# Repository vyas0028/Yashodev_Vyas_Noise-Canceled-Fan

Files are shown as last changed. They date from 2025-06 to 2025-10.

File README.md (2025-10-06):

# Noise Canceling Fan Project

A desktop fan that cancels its own noise using active noise cancellation, built utilizing CAD, embedded programming, signal processing, and acoustic analysis to create a standalone product! 

<div style="display: flex; justify-content: center; align-items: center; gap: 50px;">
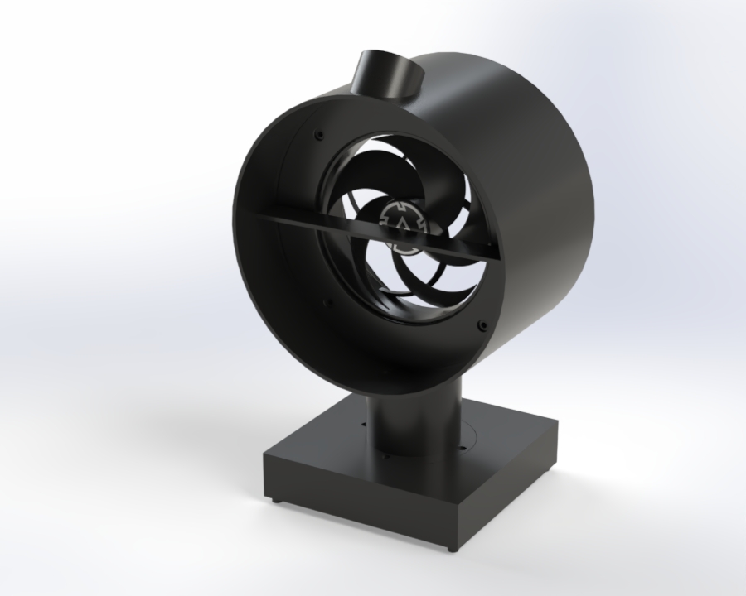
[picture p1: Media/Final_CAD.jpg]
Final CAD model of fan
  
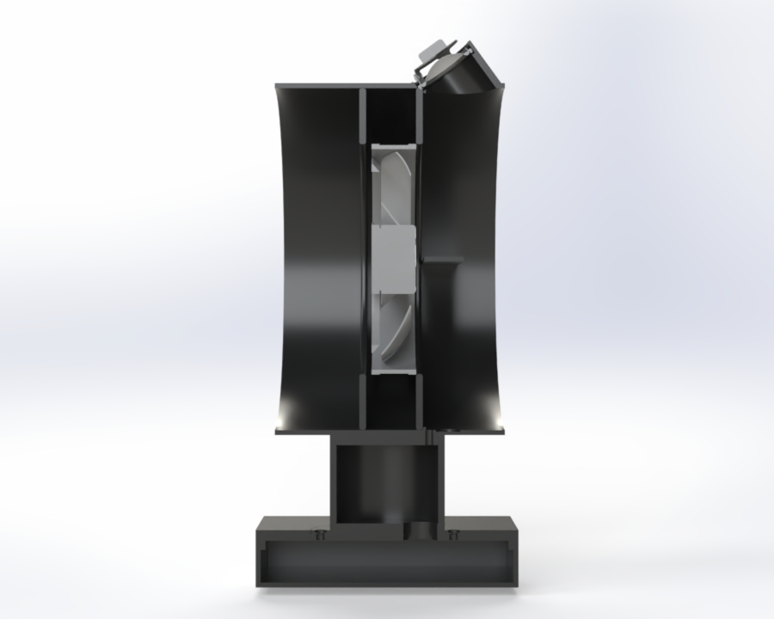
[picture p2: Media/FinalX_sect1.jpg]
Cross-section of fan CAD model
  
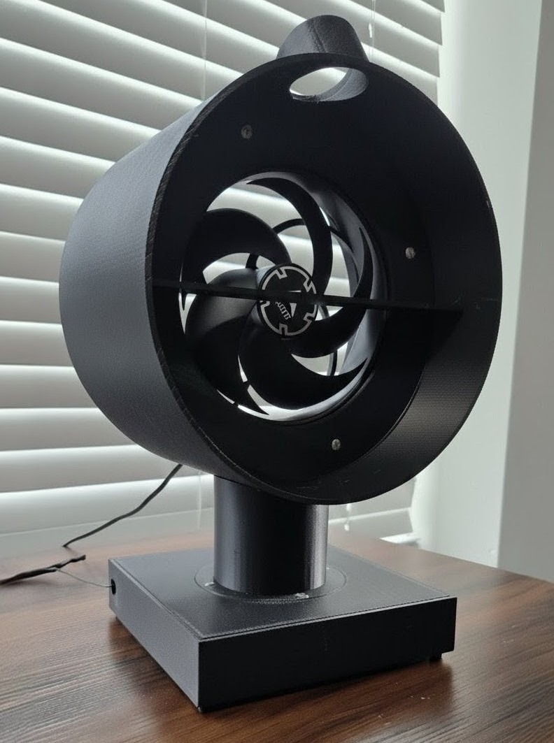
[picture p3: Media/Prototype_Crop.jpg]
Photo of physical fan prototype
  
</div>

---

## What It Does

This fan detects its own blade-generated noise using a microphone, identifies the dominant frequency using an FFT (Fast Fourier Transform), and cancels it in real time by outputting inverted sound through a speaker

---

## How it Works  
1. The microcrophone and Teensy microcontroller communicate using I2S
2. The noise data that is sent to the microcontroller from the mic is processed by an FFT (Fast Fourier Transform) in the PJRC Audio library.
   - This identifies the specific frequency of noise with the highest amplitude
4. Once the specific frequency is identified, the tone is phase shifted 180 deg and played out of the speaker using AudioConnection 
5. A simple hill-climb/coordinate descent algorithm reads the FFT again and nudges the phase + amplitude of the anti-tone up and down until a minimum is achieved.  

---

## Testing 
- Ran modal FEA to ensure that the housing doesn't resonate at the fan's blade pass frequency of 172 Hz.
    - Found main vibrational mode at 350 Hz. Well out of range for resonance.
- Conducted bench testing
    - Wired Teensy, speaker + amp, microphone, and fan together. Consolidated grounds and ensured that microphone can record audio that can be played out of the speaker. Also ensured that fan can be properly controlled via PWM. 
## Status/Next Steps
- Bench testing is now complete. All components - speaker, mic, Teensy, and fan connect to each other and are functonal on the breadboard and mechanically fit into the shroud and base. 
- Next steps will be rewiring everything into the 3D printed housing, taking decibel measurements, refining the algorithm (implement active FxLMS, possibly replace FFT with Goertzel), and creating a PCB to replace the breadboard.

---

## CAD Model Links
| [Part](link)                                                      |   Description  
| [Box](CAD/Project_CAD/box.SLDPRT)                                 |   Box that forms the base. Houses electronics.   
| [Lid](CAD/Project_CAD/lid.SLDPRT)                                 |   Lid that fits flush with top of base. Mounts to support tube with screws.  
| [Support_Tube](CAD/Project_CAD/tube.SLDPRT)                       |   Vertical support tube that rises from lid to shroud. Houses wiring.   
| [Fan_Housing_Front_Plate](CAD/Project_CAD/Fan_Front_Plate.SLDPRT) |   Circular plate that sits in front of fan to create circular profile to fit into shroud.   
| [Fan_Housing_Back_Plate](CAD/Project_CAD/Fan_Back_Plate.SLDPRT)   |   Circular plate that sits in behind fan to create circular profile to fit into shroud.   
| [Fan_Shroud](CAD/Project_CAD/Shroud.SLDPRT)                       |   Horizontal cylinder that houses fan, microphone, and speaker. Connects to support tube at bottom.      
| [Final_Assembly](CAD/Project_CAD/Final_Assembly.SLDPRT)           |   Final assembly of shroud, tubewith holes, lid, and base.

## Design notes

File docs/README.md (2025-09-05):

# Noise Canceling Fan Readme

A desktop fan that actively reduces its own noise using real-time noise cancellation. This project combines CAD, embedded programming, signal processing, and acoustic analysis to showcase the engineering process from start to finish and create a standalone product! 

<p float="left">
  
  
</p>

---

## What It Does

This fan detects its own blade-generated noise using a microphone, identifies the dominant frequency using an FFT (Fast Fourier Transform), and cancels it in real time by outputting inverted sound through a speaker

---

## How it Works  
1. The microcrophone and Teensy microcontroller communicate using I2S
2. The noise data that is sent to the microcontroller from the mic is processed by an FFT (Fast Fourier Transform) in the PJRC Audio library.
   - This identifies the specific frequency of noise with the highest amplitude
4. Once the specific frequency is identified, the tone is phase shifted 180 deg and played out of the speaker using AudioConnection 
5. A simple hill-climb/coordinate descent algorithm reads the FFT again and nudges the phase + amplitude of the anti-tone up and down until a minimum is achieved.  

---

## Status/Next Steps
- Bench testing is now complete. All components - speaker, mic, Teensy, and fan connect to each other and are functonal on the breadboard and mechanically fit into the shroud and base. 
- Next steps will be rewiring everything into the 3D printed housing, taking decibel measurements, refining the algorithm (implement active FxLMS, possibly replace FFT with Goertzel), and creating a PCB to replace the breadboard.

---

## CAD Model Links
| [Part](link)                                                      |   Description  
| [Box](CAD/Project_CAD/box.SLDPRT)                                 |   Box that forms the base. Houses electronics.   
| [Lid](CAD/Project_CAD/lid.SLDPRT)                                 |   Lid that fits flush with top of base. Mounts to support tube with screws.  
| [Support_Tube](CAD/Project_CAD/tube.SLDPRT)                       |   Vertical support tube that rises from lid to shroud. Houses wiring.   
| [Fan_Housing_Front_Plate](CAD/Project_CAD/Fan_Front_Plate.SLDPRT) |   Circular plate that sits in front of fan to create circular profile to fit into shroud.   
| [Fan_Housing_Back_Plate](CAD/Project_CAD/Fan_Back_Plate.SLDPRT)   |   Circular plate that sits in behind fan to create circular profile to fit into shroud.   
| [Fan_Shroud](CAD/Project_CAD/Shroud.SLDPRT)                       |   Horizontal cylinder that houses fan, microphone, and speaker. Connects to support tube at bottom.      
| [Final_Assembly](CAD/Project_CAD/Final_Assembly.SLDPRT)           |   Final assembly of shroud, tubewith holes, lid, and base.

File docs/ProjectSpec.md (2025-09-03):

## Welcome to the Noise Canceling Fan Project Specification! This is a a summary of general project parameters. 

## Project Overview
A desktop fan assembly that actively cancels its own noise by collecting noise signal using MEMS microphone, conducting FFT on a Teensy microcontroller, and then outputting an inverted signal through a speaker to cancel fan whine. 

---

## Design Inputs
- Microphone must detect fan noise frequencies and communicate with Teensy. 
- Teensy must perform real-time FFT and generate inverted wave through speaker.
- The fan must fit snugly into a circular chamber.
- The base must allow for a breadboard/pcb to sit inside.
- There must be a way to prevent direct feedback from the speaker into the mic.

---

## Performance Targets

| Metric | Target Value |
|---|---|
| SPL Reduction (@ mic) | ≥ 4 dB |
| Fan Speed Range | 200–1700 RPM |
| FFT Latency | ≤ 50 ms |

---

## Mechanical Spec
- **Fan**: 140 mm ARCTIC P14 PWM, enclosed in horizontal cylindrical shell
- **Support**: Cylindrical post connecting fan shell to base
- **Base**: 120 × 120 × 30 mm rectangular platform with hollow interior
- **Mic**: Top surface of base, centered in front of fan
- **Speaker**: Front face of base in circular cutout
- **Feet**: 4 corner supports with rubber bottoms for grip

---

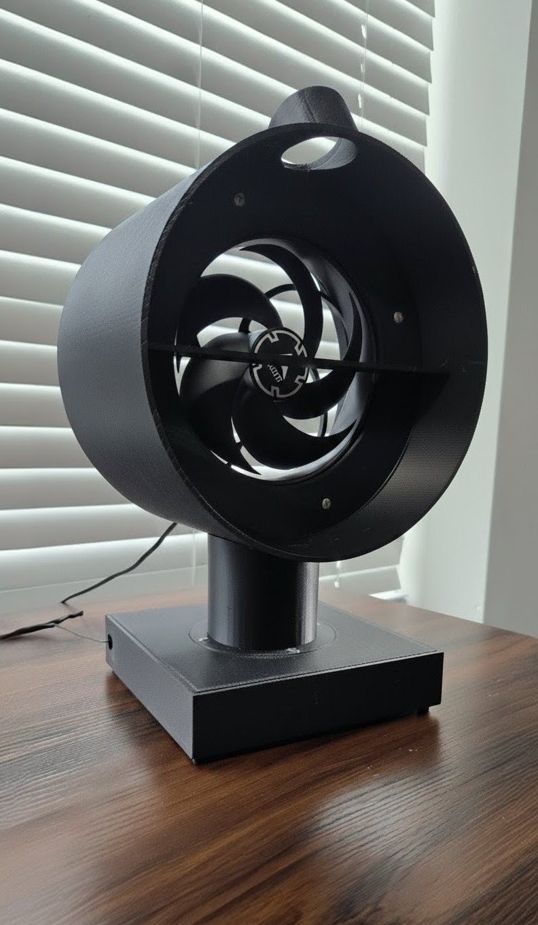
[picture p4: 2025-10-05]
Media/Prototype.jpg

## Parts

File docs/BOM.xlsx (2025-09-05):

Item # | Part / Description | Manufacturer | Part # | Qty | Unit Price (USD) | Vendor Link | Status
1 | Teensy 4.1 (with headers) | PJRC | TEENSY41 | 1 | 29.95 | https://www.pjrc.com/store/teensy41.html | Ordered
2 | INMP441 MEMS I²S Microphone Module (5‑pack) | InvenSense | INMP441‑MOD | 1 | 7.99 | https://www.amazon.com/dp/B086KQ4DLG | Ordered
3 | MAX98357A I²S Class‑D Audio Amp (4‑pack) | Maxim/ADI | MAX98357A‑MOD | 1 | 8.89 | https://www.amazon.com/dp/B075N8248Q | Ordered
4 | 40 mm 4 Ω 3 W Full‑Range Speaker (pair) | Gikfun | EK1794 | 1 | 6.99 | https://www.amazon.com/dp/B01L8GHB7O | Ordered
5 | ARCTIC P14 PWM PST 140 mm Fan | Arctic | ACFAN00137A | 1 | 10.99 | https://www.amazon.com/dp/B07GJZG3RZ | Owned
6 | 12 V 2 A DC Power Adapter (barrel jack) | HighPot | 12V2A‑ADP | 1 | 8.49 | https://www.amazon.com/dp/B01MEF5MHQ | Owned
7 | Barrel Jack to Screw Terminal Adapter | Uxcell | 214‑BJ‑ST | 1 | 4.99 | https://www.amazon.com/dp/B07WJ3N2ZK | Ordered
8 | USB‑C Wall Brick 5 V 2 A + Cable | Anker | A2017 | 1 | 11.99 | https://www.amazon.com/dp/B07THHQMHM | Owned
9 | Breadboard + Jumper Wires | Elegoo | EL‑CP‑004 | 1 | 6.99 | https://www.amazon.com/dp/B01EV70C78 | Owned
10 | M3 Heat‑Insert Brass Inserts (50 pcs) | E‑Sun | M3‑INS‑50 | 1 | 9.99 | https://www.amazon.com/dp/B07B4WPNJF | Planned
11 | Rubber Feet, 12 mm (set of 4) | 3M | SJ5303 | 1 | 3.5 | https://www.amazon.com/dp/B0006HVMGQ | Planned

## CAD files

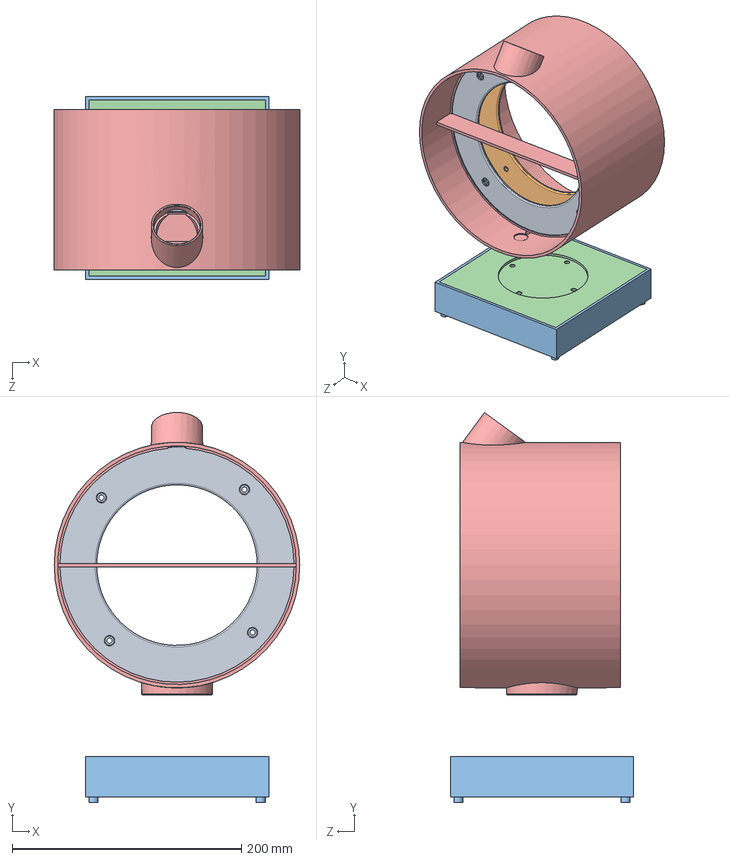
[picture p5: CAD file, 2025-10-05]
CAD/Project_CAD/Assemblies/FINAL_assembly.SLDASM
214.3 x 340.4 x 160.0 mm
Shroud
lid
Fan_Back_Plate
Fan_Front_Plate

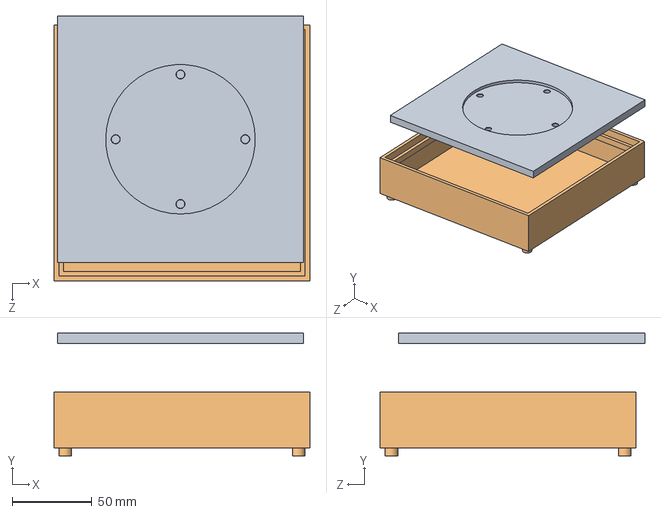
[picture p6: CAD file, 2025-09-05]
CAD/Project_CAD/Assemblies/box+lid_for_Image.SLDASM
160.0 x 76.9 x 165.5 mm
lid

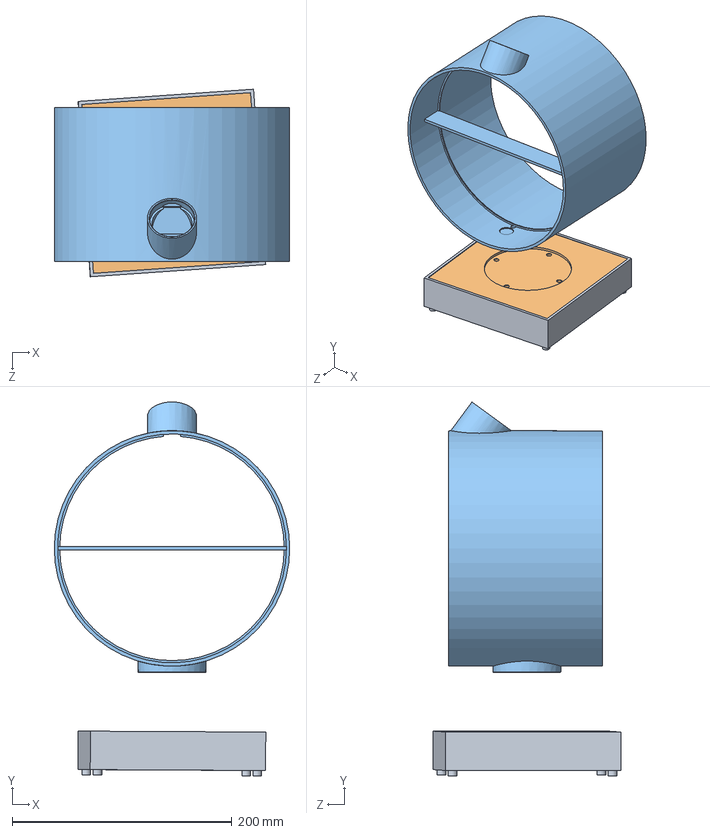
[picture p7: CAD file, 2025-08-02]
CAD/Project_CAD/Test_Assembly.SLDASM
214.3 x 340.4 x 170.7 mm
Shroud
lid

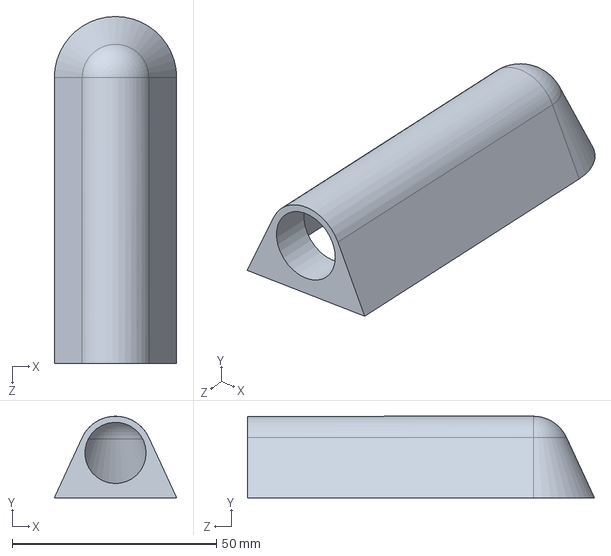
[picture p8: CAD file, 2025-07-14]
CAD/Practice_CAD/Practice_Lampshade.SLDPRT
30.0 x 20.0 x 85.0 mm

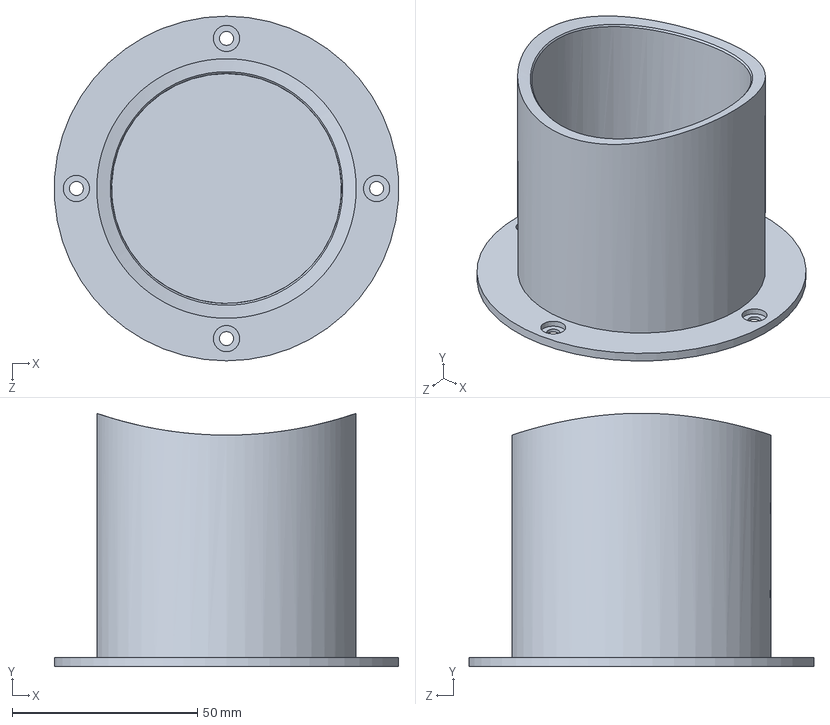
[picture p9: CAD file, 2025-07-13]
CAD/Project_CAD/Parts_For_Printing/Tube+shroud.SLDPRT
92.8 x 68.4 x 93.0 mm

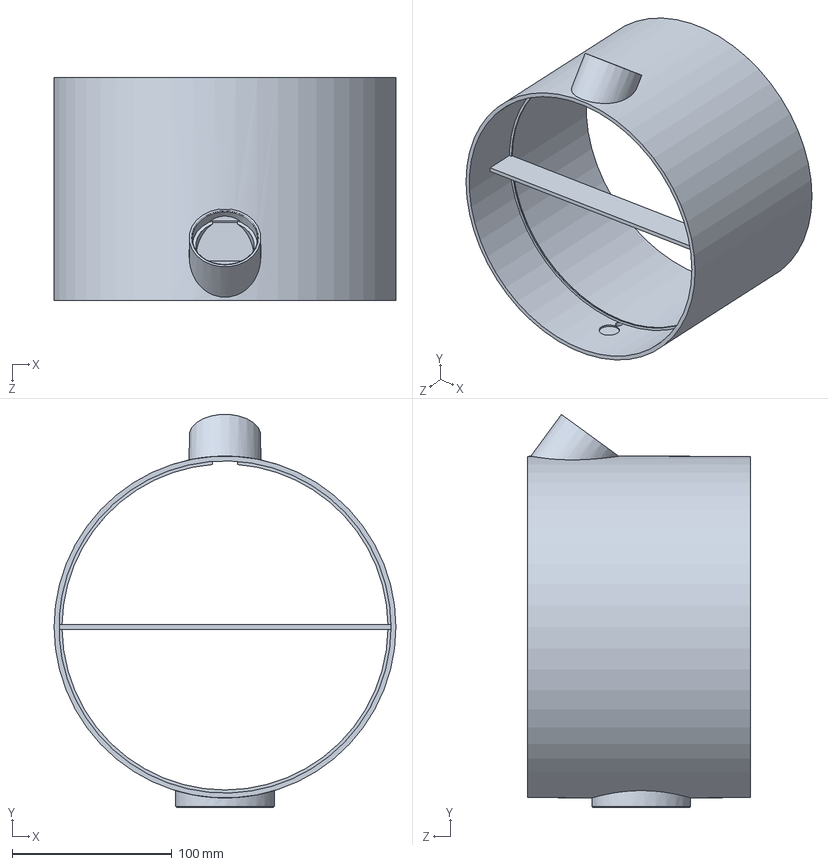
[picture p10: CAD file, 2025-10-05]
CAD/Project_CAD/Shroud.SLDPRT
214.3 x 246.4 x 140.0 mm

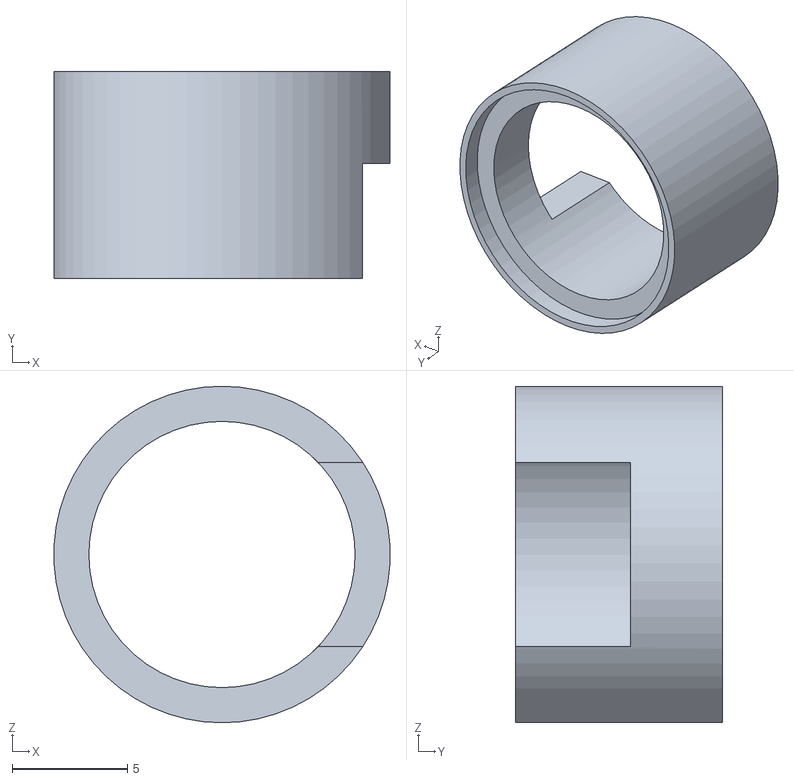
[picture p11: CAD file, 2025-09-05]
CAD/STL_Files/Mic_Fixture.STL
14.6 x 9.00 x 14.6

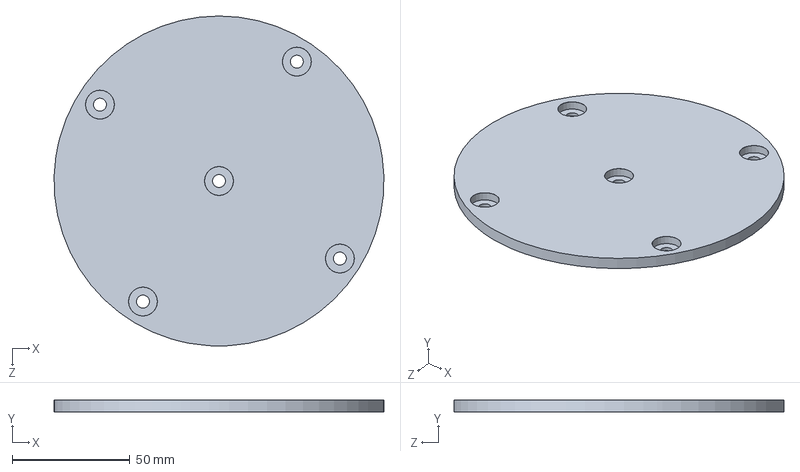
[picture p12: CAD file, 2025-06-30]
CAD/Practice_CAD/Practice_Plate.SLDPRT
139.9 x 5.00 x 140.0 mm

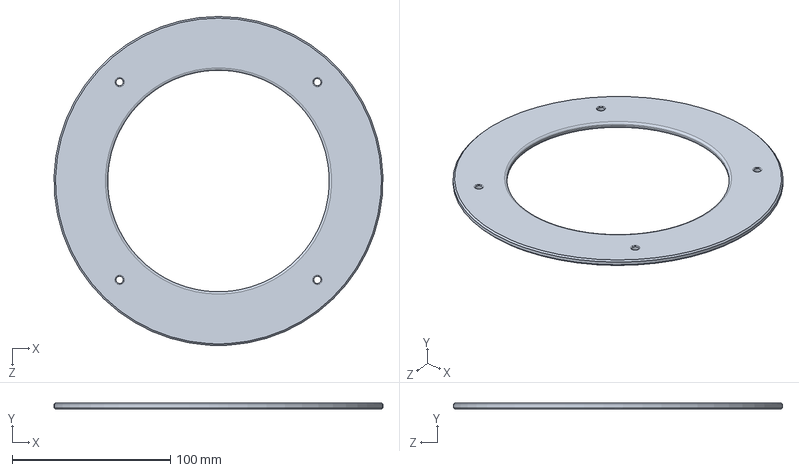
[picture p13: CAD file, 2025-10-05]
CAD/Project_CAD/Fan_Back_Plate.SLDPRT
207.9 x 4.00 x 208.0 mm

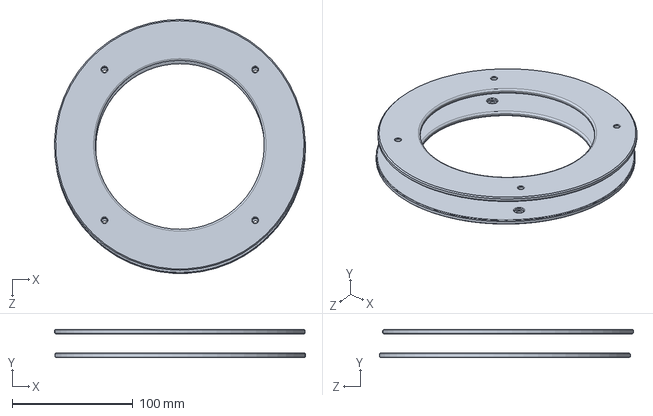
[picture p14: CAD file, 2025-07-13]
CAD/Project_CAD/Parts_For_Printing/Assem8.SLDPRT
208.2 x 23.6 x 210.7 mm

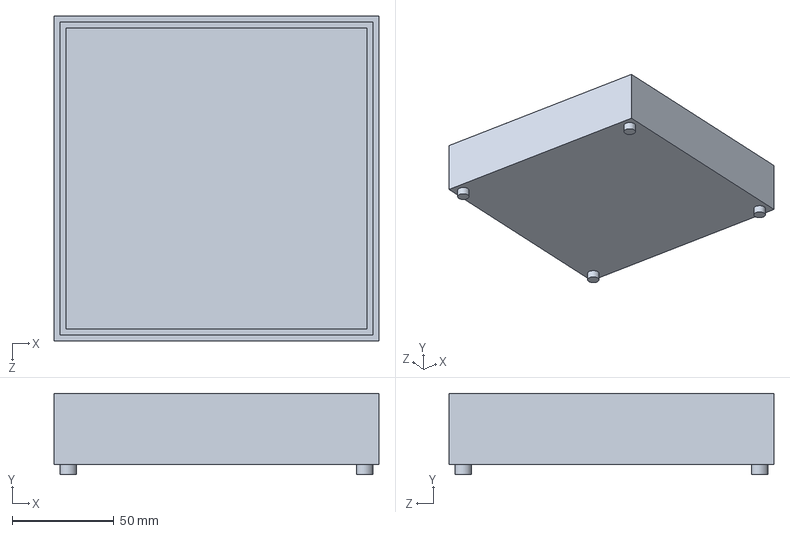
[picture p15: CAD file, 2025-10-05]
CAD/Project_CAD/box.SLDPRT
160.0 x 40.0 x 160.0 mm

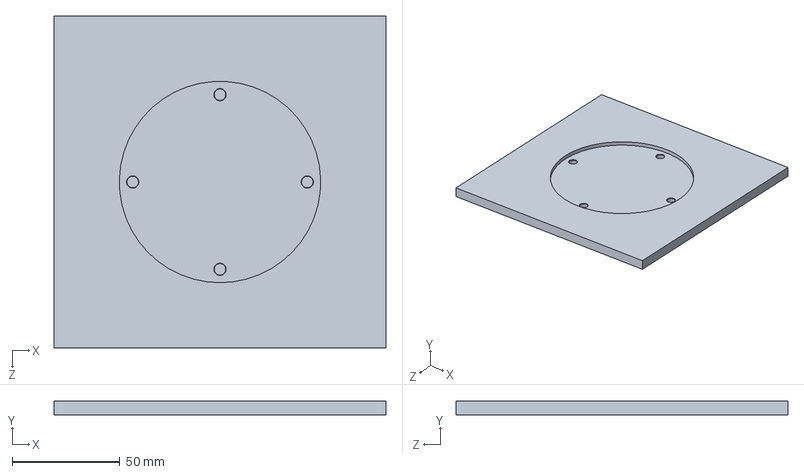
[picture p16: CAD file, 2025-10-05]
CAD/Project_CAD/lid.SLDPRT
154.0 x 6.50 x 154.0 mm

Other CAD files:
CAD/Project_CAD/Assemblies/X_section.SLDASM
CAD/STL_Files/tube.STL
CAD/STL_Files/Fan_Back_Plate.STL
CAD/Project_CAD/Fan_Front_Plate.SLDPRT
CAD/STL_Files/box.STL
CAD/Project_CAD/Mic_Fixture.SLDPRT
CAD/Project_CAD/tube.SLDPRT
CAD/STL_Files/Assem2.SLDPRT
CAD/STL_Files/Assem8.STL
CAD/STL_Files/Fan_Front_Plate.STL
CAD/STL_Files/Shroud.STL
CAD/STL_Files/lid.STL

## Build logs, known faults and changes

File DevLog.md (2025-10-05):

# Noise-Canceling Fan Devlog

Welcome to the Noise-Canceling Fan DevLog! This is a running summary of daily work on this project.

---

## 06-29-2025

**Done**  
- Created Repo and README  
- Brainstormed high-level design: 3D printed hollow rectangular base with four supports, speaker on the front face, microphone hole on the top face, fan housed in horizontal cylinder supported by cylindrical column from base. Electrical housed under the base.

**Learned**  
- GitHub repo organizations for engineering projects.

**Next**  
- Order parts (mic, speaker, Teensy, etc), CAD practice, write project specifications.

---

## 06-30-2025

**Done**  
- Ordered parts (microcontroller, fan, electronics)

**Learned**  
- Electronics required (amplifier module, barrel jack adapter, etc)

**Next**  
- Write spec, BOM, CAD practice

---

## 07-02-2025

**Done**  
- Got hung up on internship work. Watched one SolidWorks recap video.

**Next**  
- CAD practice, first models.

---

## 07-03-2025

**Done**  
- Completed SolidWorks recap video

**Learned**  
- Reviewed SolidWorks basics (sketching, boss/revolve, shell, fillet)

**Next**  
- Begin practice parts

---

## 07-06-2025

**Done**  
- Created horizontal “lampshade” example from SolidWorks part modeling tutorial utilizing sketch, extrude, extrude-cut, shell, and fillet.  
  - [Practice_Lampshade.SLDPRT](../CAD/Practice_CAD/Practice_Lampshade.SLDPRT)  
- Created circular baseplate to practice HoleWizard  
  - [Practice_Plate.SLDPRT](../CAD/Practice_CAD/Practice_Plate.SLDPRT)

<p float="left">
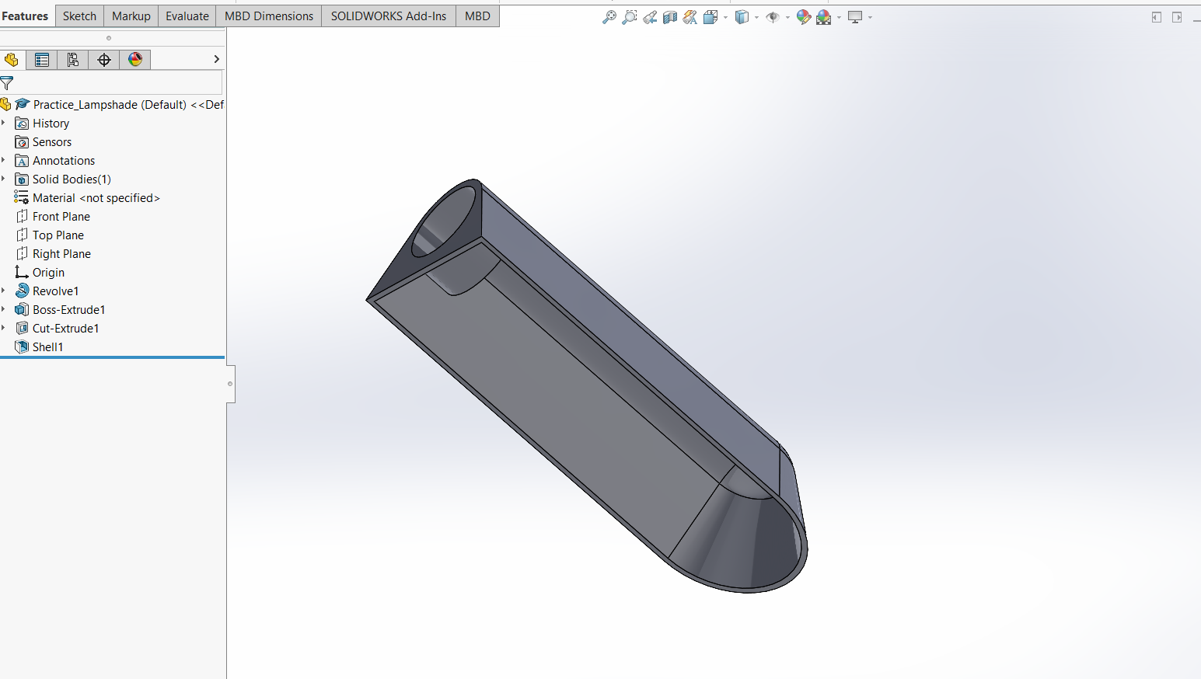
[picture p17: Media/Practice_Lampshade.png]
  
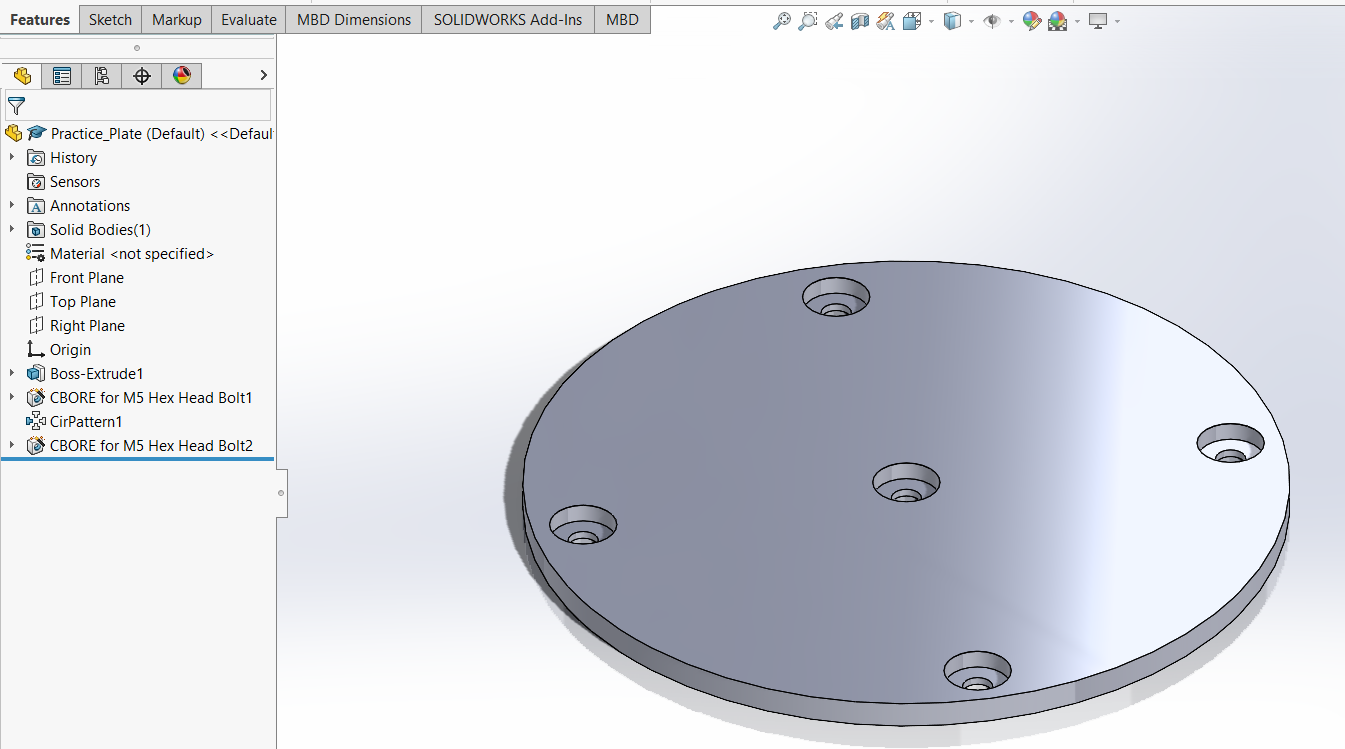
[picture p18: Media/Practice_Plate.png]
  
</p>

**Learned**  
- More thorough review of SolidWorks basics and learned about HoleWizard.

**Next**  
- Continue practice parts

---

## 07-07-2025

**Done**  
- Revisited design. Original model with speaker on front of base was deemed nonfunctional. Learned that noise canceling needs good alignment of fan noise to noise canceling output from speaker. Redesigned to include speaker pointing directly into cylindrical fan shroud. Brainstormed horizontal plate that separates direct line of sight from speaker to mic inside shroud chamber.

**Learned**  
- [AMCA Basics of Fan Noise Presentation](https://www.amca.org/assets/resources/public/assets/uploads/FINAL-_AMCA_Fan_Noise_RG.pdf)  
- [Noise Canceling Case Study](https://www.diva-portal.org/smash/get/diva2%3A831430/FULLTEXT01.pdf)  
-  Design requires **iteration**. Every single idea/design will have issues that come up and need to be addressed.

**Next**  
- Begin CAD for base, support tube, and shroud

---

## 07-09-2025

**Done**  
- Began base: 160 × 160 × 25 mm with a 5.5 mm thick lip running along the inner face of box for lid to sit flush.

<p float="left">
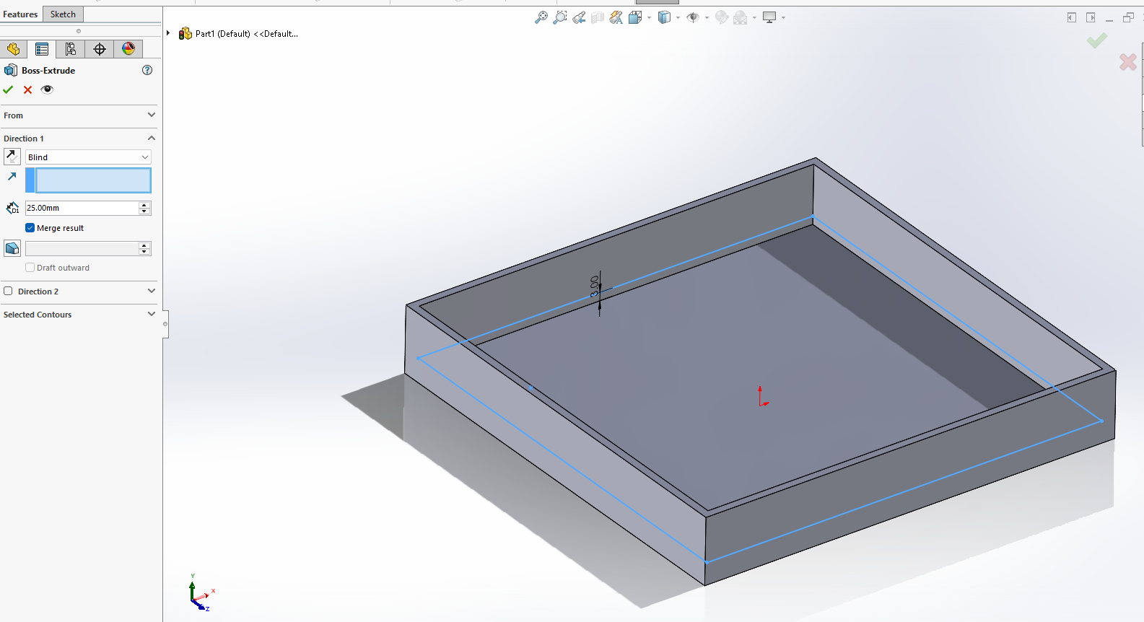
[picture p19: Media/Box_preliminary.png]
  
</p>

**Learned**  
- How to insert planes.

**Next**  
- Continue CAD for base, begin support tube, cylindrical shroud, round sleeve for fan.

---

## 07-12-2025

**Done**  
- Completed prelim design for base box. Used cut extrude from various planes within the box to create a lip on inside edge that will allow lid to sit flush with top.

<p float="left">
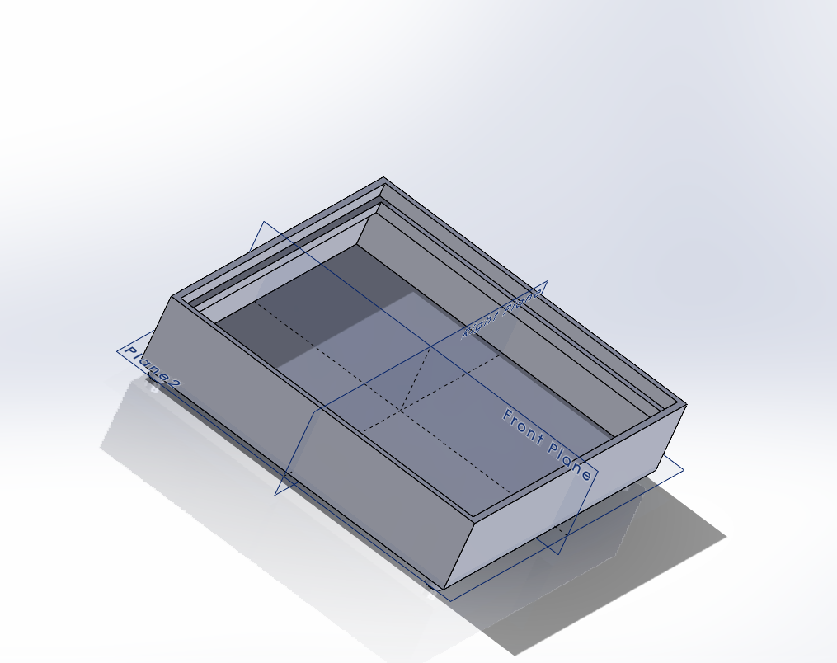
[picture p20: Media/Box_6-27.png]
  
</p>

**Learned**  
- Learned how to insert plane at specific height. 

**Next**  
- Begin CAD for lid, support tube, and shroud.

---

## 07-15-2025

**Done**  
- Completed design for lid (157.5 × 157.5 × 6.5 mm). Thickness allows flange from tube to sit into lid comfortably.
- Completed design for support tube: 70 × 70 mm cylinder with 3 mm wall thickness. Added 82 mm diameter, 2.5 mm thick flange around bottom of tube. Added 82 mm diameter, 2.5 mm deep recess into lid to allow tube to fit. Added four M4 tapped holes on a 76 mm diameter circle to flange, and clearance holes for brass inserts.

<p float="left">
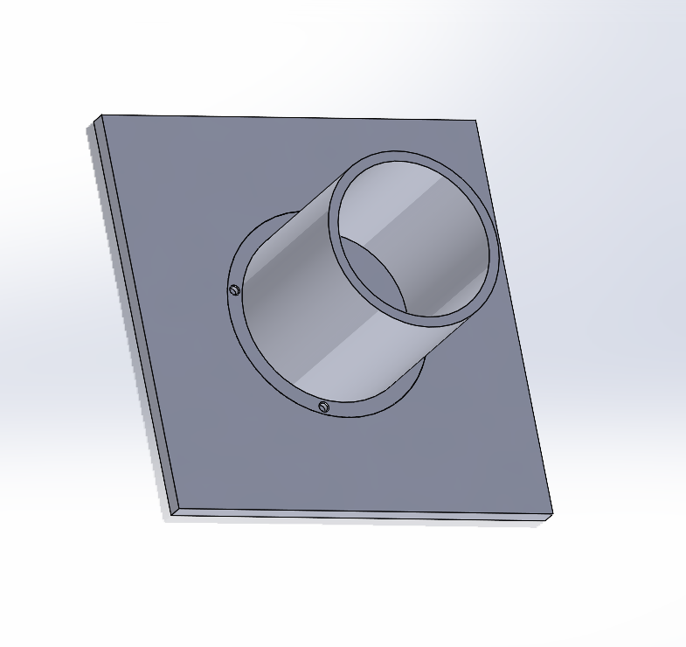
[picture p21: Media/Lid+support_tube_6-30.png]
  
</p>

**Learned**  
- Refreshed skills with basic extrude. Began GD&T, designing one part to fit into another.  
- Refreshed skills with HoleWizard. Learned screw size selection and technique for press fitting brass inserts.

**Next**  
- Begin CAD for fan housing plates and shroud

---

## 07-18-2025

**Done**  
- Created circular plates for front and back of fan to fit into cylindrical shroud.   
  - OD: 208 mm, thickness: 4 mm.  
  - Hole pattern: 4 × 4.45 mm holes on 124 × 124 mm square. Front plate counterbored (Ø 8 mm) for flush screws. Back plate holes Ø 5.7 mm × 3.5 mm deep with 0.5 mm skin for brass inserts.  
  - Central cutout: Ø 140 mm, filleted inner edges, chamfered outer edges (0.5 mm × 45°).
  - [Fan_Front_Plate.SLDPRT](../CAD/Project_CAD/Fan_Front_Plate.SLDPRT)  
  - [Fan_Back_Plate.SLDPRT](../CAD/Project_CAD/Fan_Back_Plate.SLDPRT)

<p float="left">
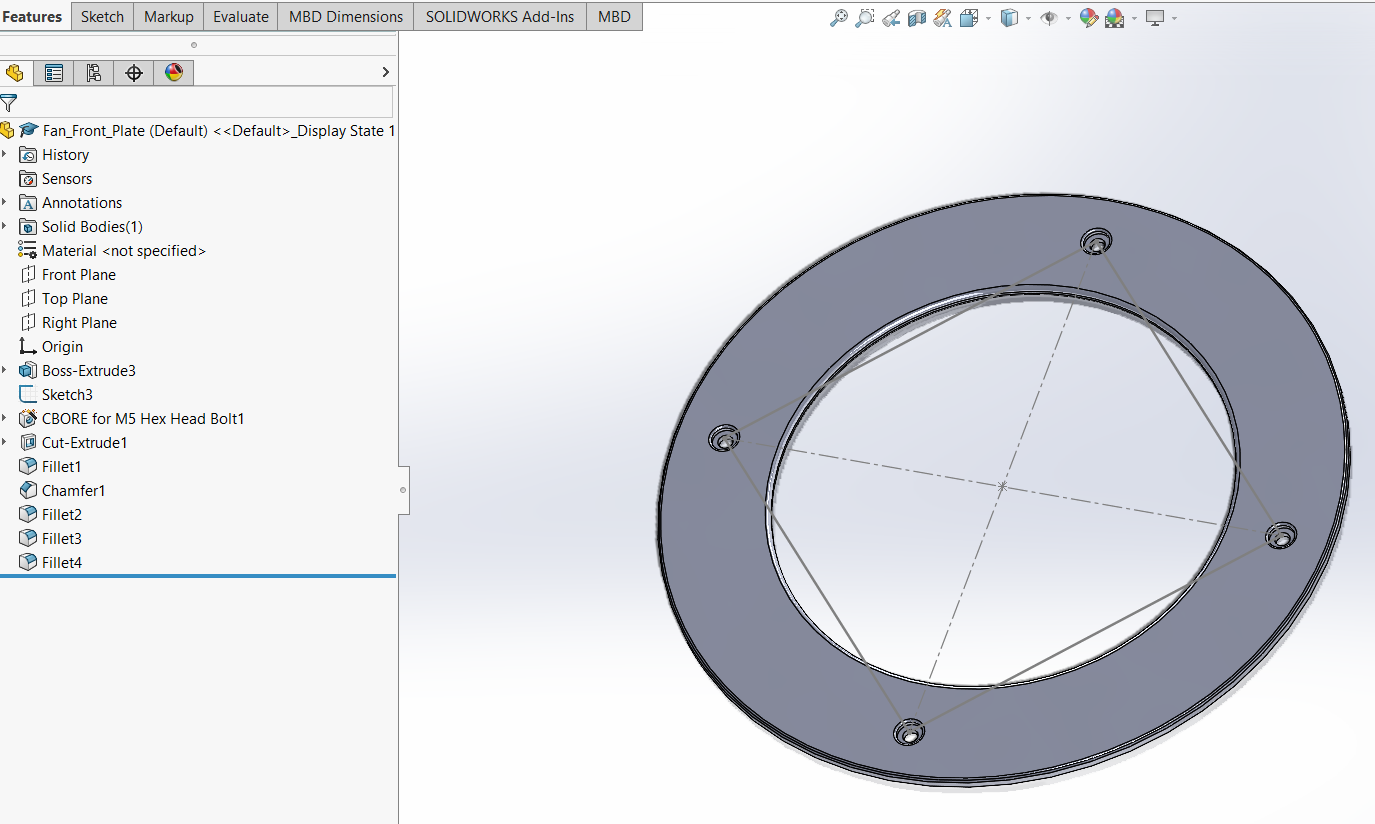
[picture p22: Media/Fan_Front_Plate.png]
  
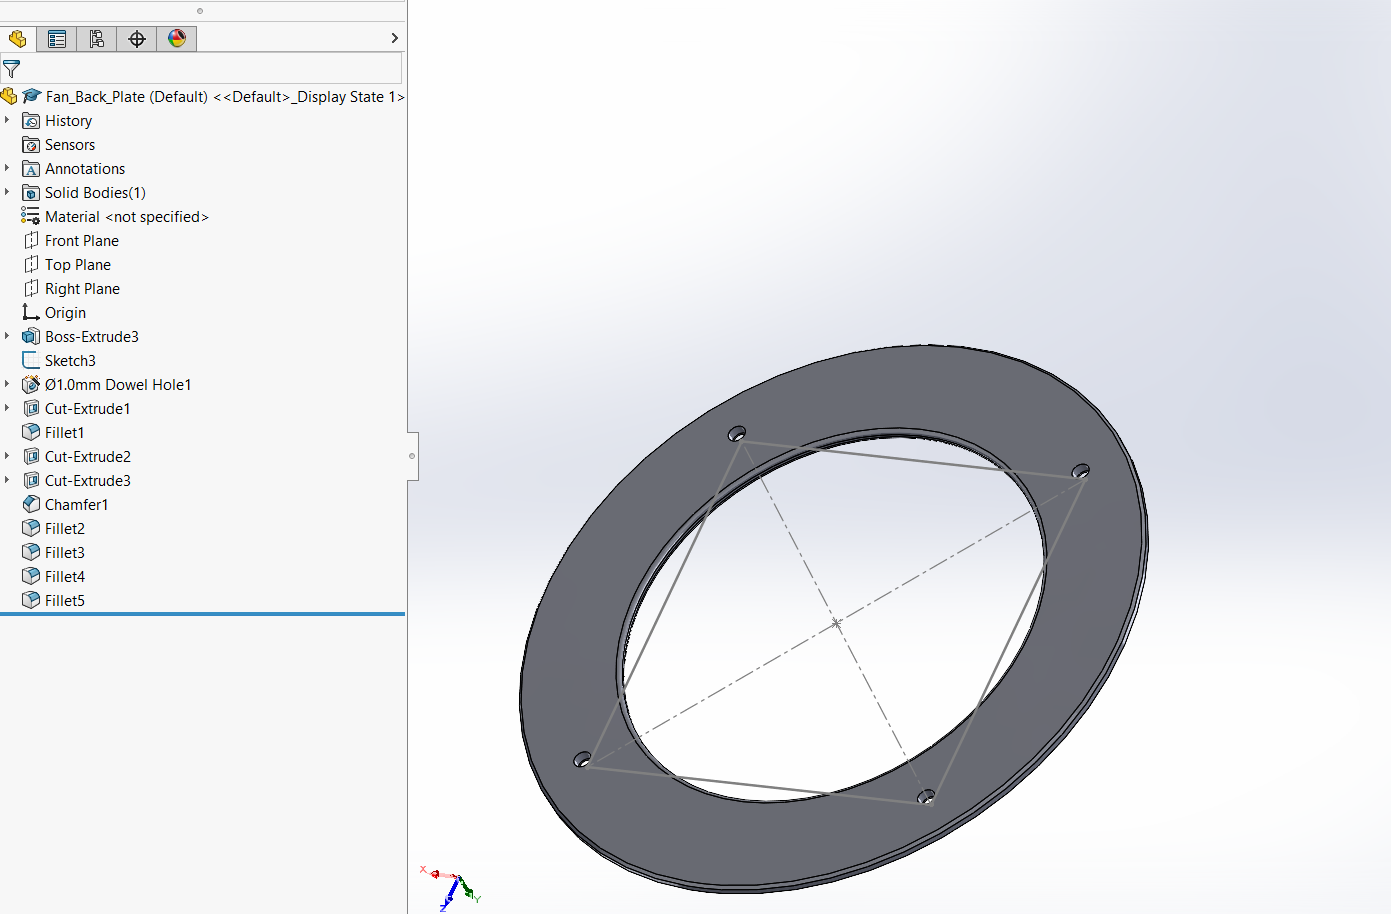
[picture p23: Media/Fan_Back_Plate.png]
  
</p>

**Learned**  
- How to apply real-world dimensions (fan specs) to a CAD problem.

**Next**  
- Begin CAD for shroud.

---

## 07-21-2025

**Done**  
- Revisited box design: inner lip was only 3.5 mm, not 6.5 mm. Revised box depth to 35 mm. Fixed wall thickness (3 mm intended) by revising lid to 153.5 × 153.5 mm and changing extrude cut dimensions on box.
- Added cylindrical 8mm support feet to box base for rubber feet coverings.  
- Began shroud development: finalized component dimensions within shroud (baffle, speaker, mic, plates, stopper ring). Shroud thickness: 3 mm.  
- [Box_FINAL.SLDPRT](../CAD/Project_CAD/Box.SLDPRT)

<p float="left">
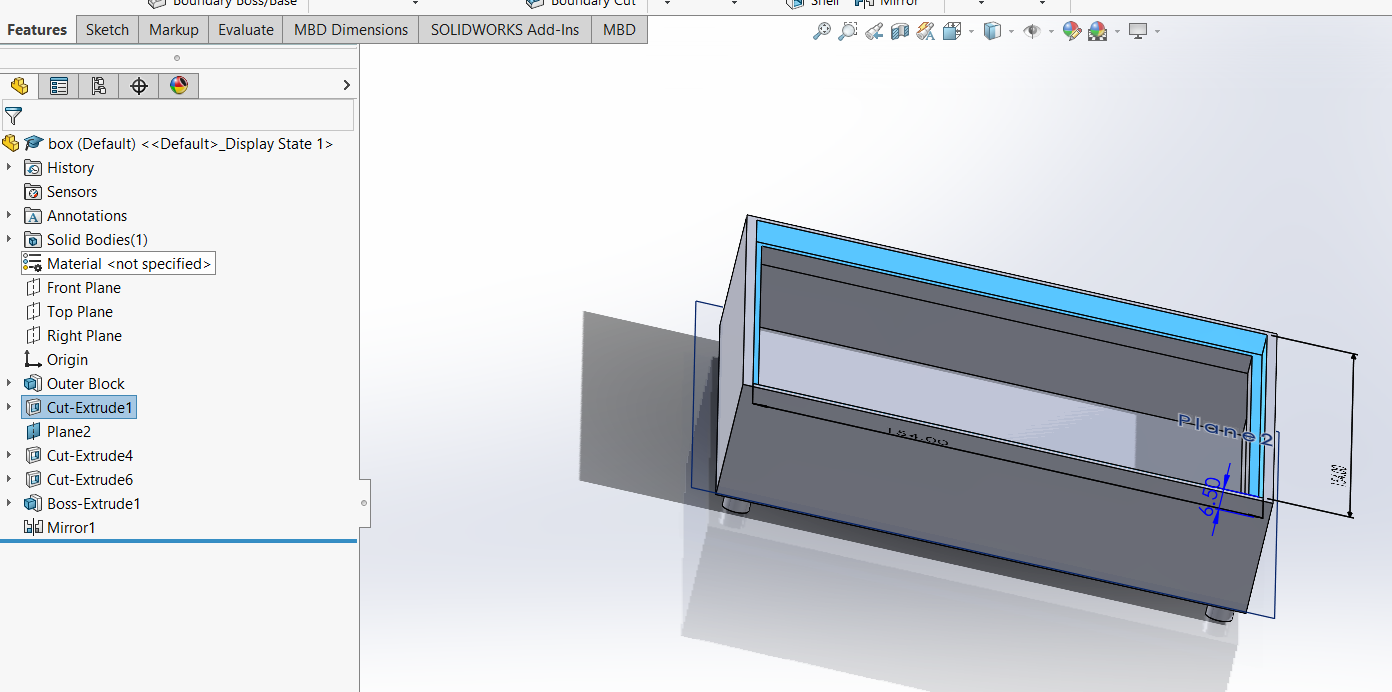
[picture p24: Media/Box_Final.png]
  
</p>

**Learned**  
- Revisiting previously completed parts is important—design and dimensions may change based on interactions.

**Next**  
- Continue shroud development and figure out mate with vertical tube.

---

## 07-23-2025

**Done**  
- Cleaned up project documentation. Filled in missing entries.

**Next**  
- Continue shroud development and figure out mate with vertical tube.

---

## 07-26-2025

**Done**  
- Further developed shroud design. Created baffle that blocks direct line of sight from speaker at top of shroud to mic at bottom. Drafted speaker hole on top of shroud: created boss on angled plane, then extruded cut flush to create speaker pocket.

<p float="left">
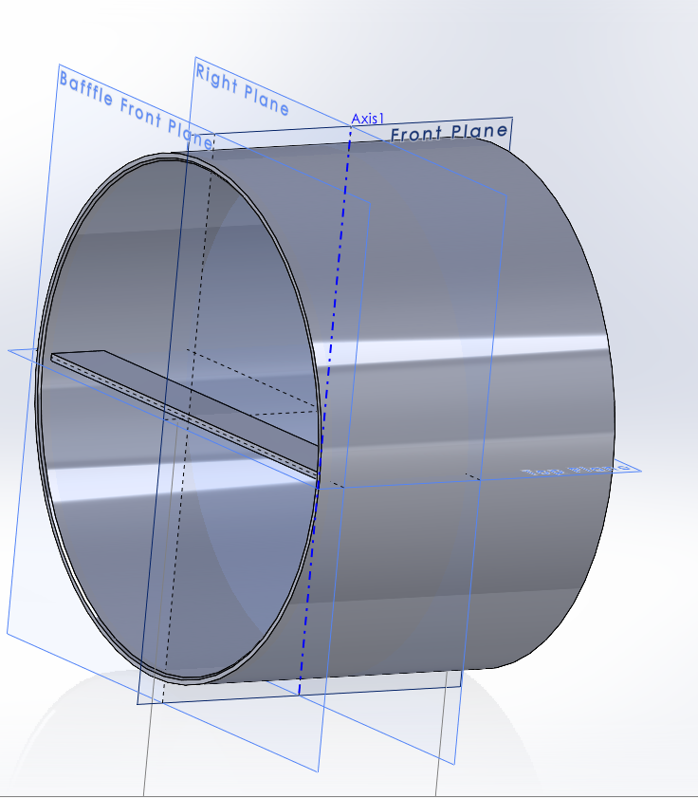
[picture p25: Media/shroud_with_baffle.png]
  
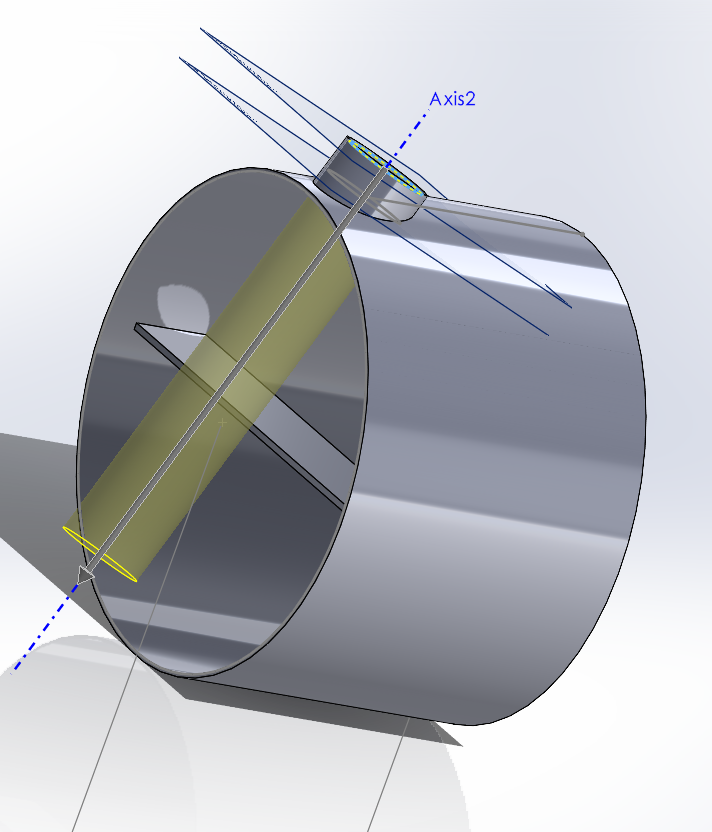
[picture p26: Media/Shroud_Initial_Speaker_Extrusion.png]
  
</p>

**Learned**  
- How to angle planes and insert reference features (axes, planes) in relation to other features.

**Next**  
- Continue shroud development and figure out mate with vertical tube.

---

## 07-27-2025

**Done**  
- Further developed shroud design. Finalized extruded cut to form speaker ledge within top extrusion. Ensured that a 60 degree projection from the fan center does not hit the shielding baffle. This prevents reflection and excess vibrations. Reflections and subsequent comb filtering can result in reverberations and poor ANC.

<p float="left">
  
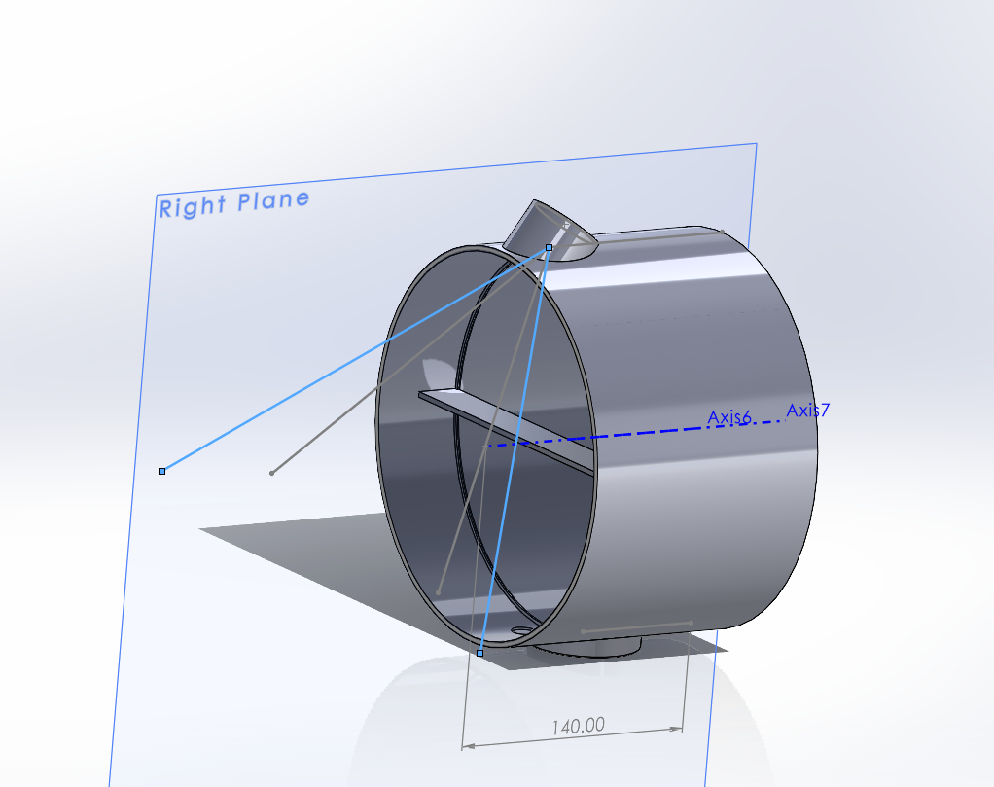
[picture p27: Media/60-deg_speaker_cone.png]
  
</p>

**Learned**  
- [Basics of comb filtering](https://www.dpamicrophones.com/mic-university/audio-production/the-basics-about-comb-filtering-and-how-to-avoid-it/).  
- Reflections and reverberations are harmful.

**Next**  
- Continue shroud development and figure out mate with vertical tube.

---

## 07-28-2025

**Done**  
- Further developed shroud design. Finalized extruded cut to form speaker ledge within top extrusion. Ensured that a 60 degree projection from the fan center does not hit the shielding baffle.  

<p float="left">
  
  
</p>

**Learned**  
- [Basics of comb filtering](https://www.dpamicrophones.com/mic-university/audio-production/the-basics-about-comb-filtering-and-how-to-avoid-it/).  
- Reflections and reverberations are harmful.

**Next**  
- Continue shroud development and figure out mate with vertical tube.

---

## 07-30-2025

**Done**  
- Finalized shroud design. Added 15 mm diameter circular recess in bottom of shroud for microphone array. Extrude cut hole for microphone wiring that goes into tube and down into base. Decided on two piece shroud and tube. Shroud has extrusion on the bottom that fits into the tube and will be glued.
- Compiled tube and shroud into an assembly. Changed extrusion of tube to "up to next" to get it flush with the shroud.

<p float="left">
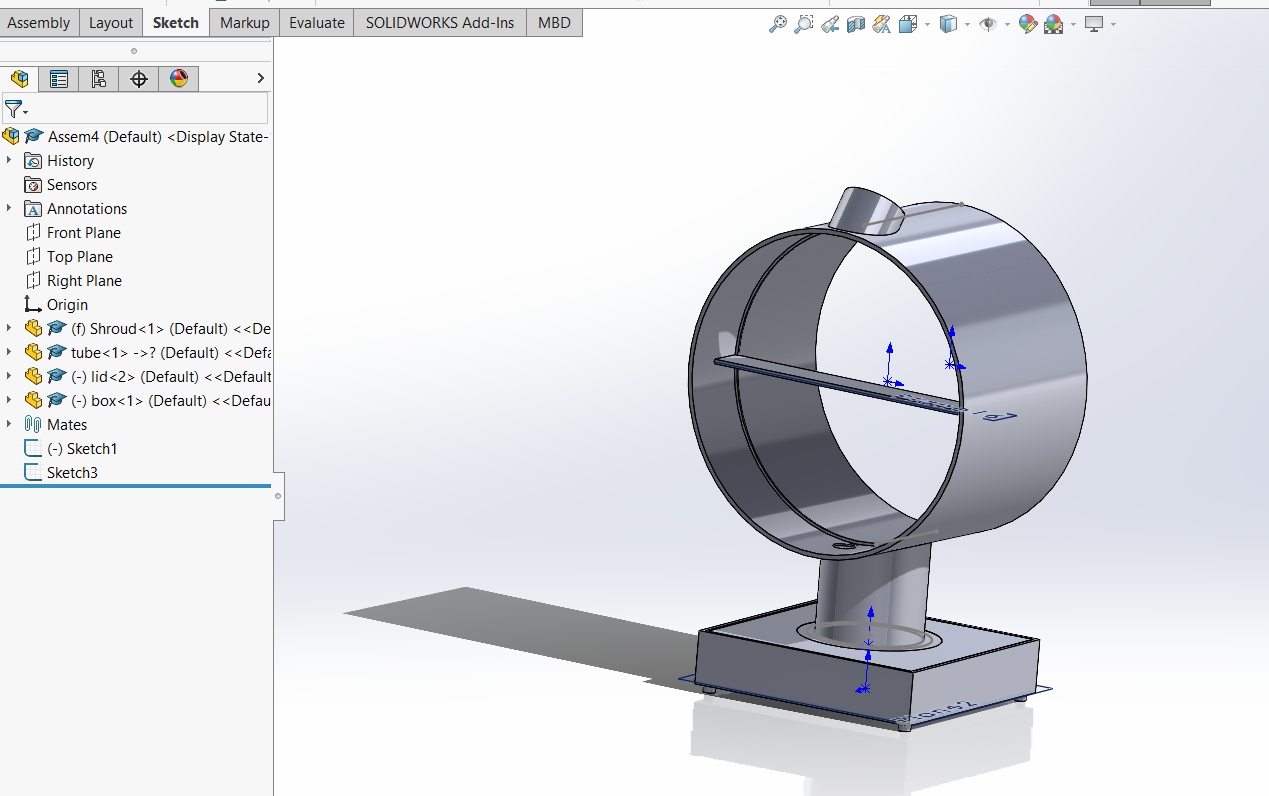
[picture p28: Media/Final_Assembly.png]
  
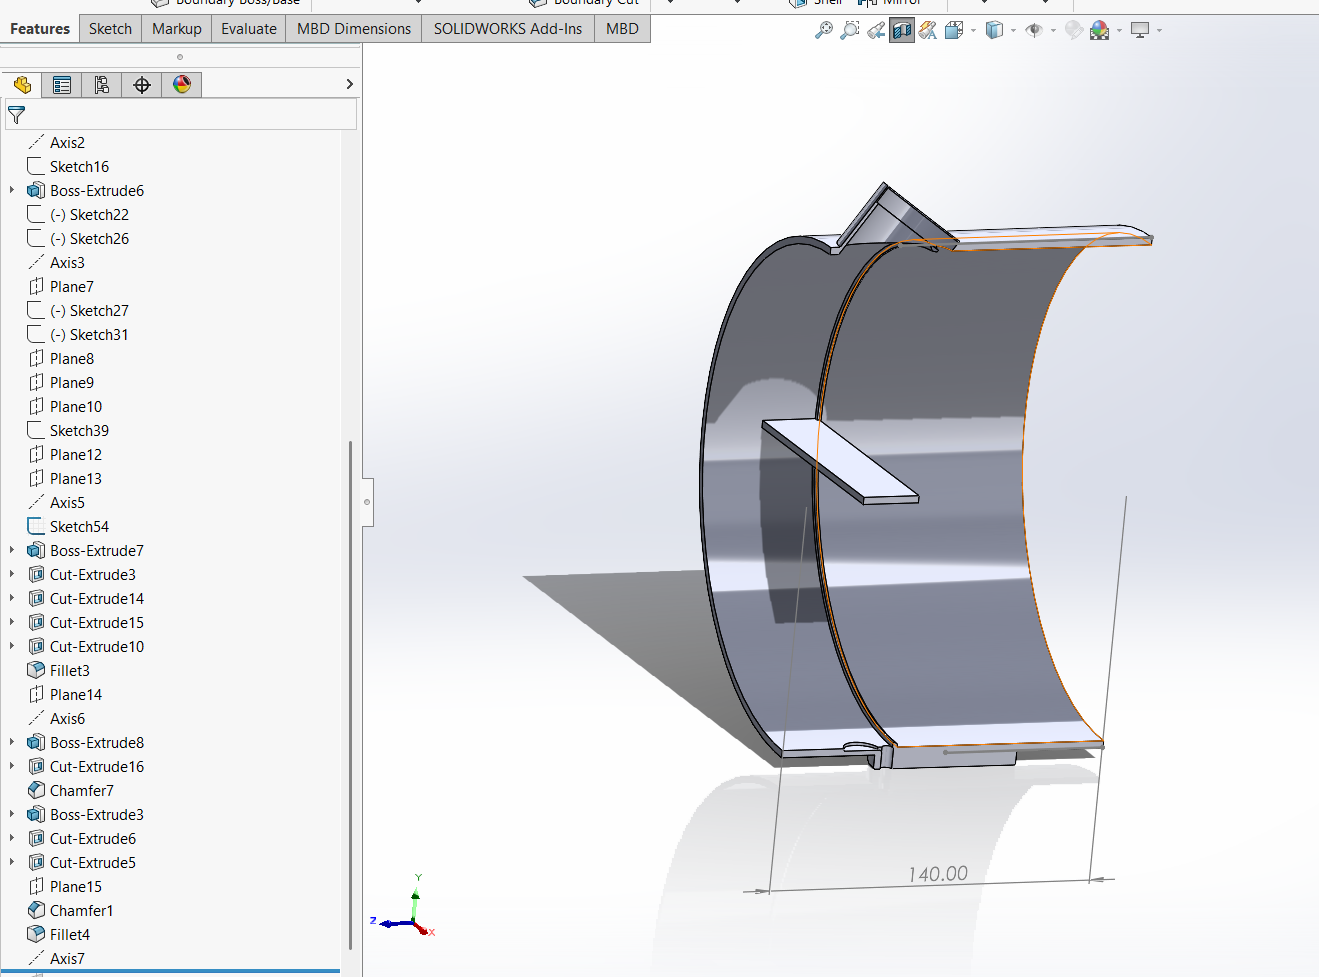
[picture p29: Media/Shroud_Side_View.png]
  
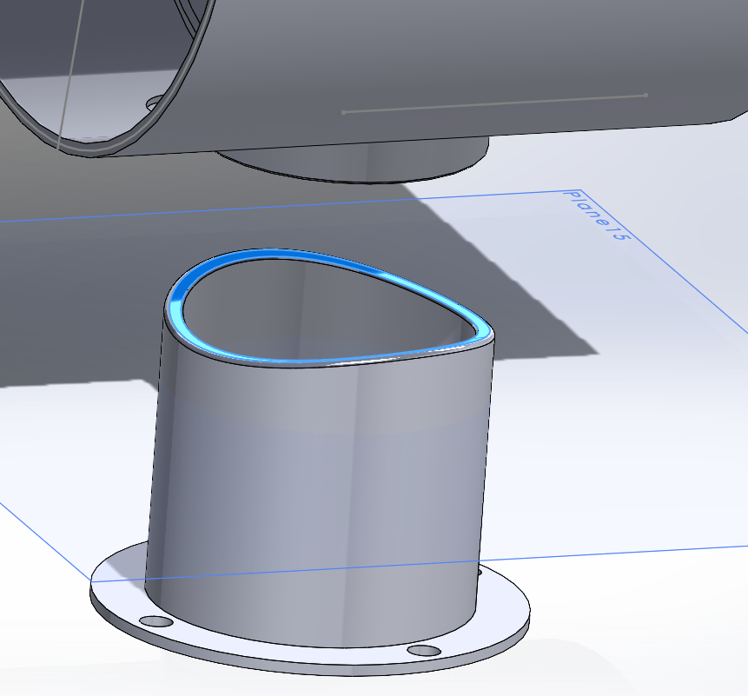
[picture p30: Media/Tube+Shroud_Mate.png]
  
</p>

**Learned**  
- Extrude "up to next" is very useful for getting features flush with one another.  
- Consulted coworker on one piece vs two piece shroud + tube. One piece would have wasted a lot of support material.

**Next**  
- Continue Prints!

---

## 08-02–08-08-2025

**Done**  
- On vacation, updated resume, documentation. 

---

## 08-10-2025

**Done**  
- Retrieved prints and physically fit together lid and base. Lid was slightly smaller than base lip area, so purchased set screw from Menards and heat set insert into base.
- Began print of shroud and initial tube.

**Learned**  
- Asked R&D Technician at my internship about tolerance and sizing issue:
  - Even though GD&T is conducted on CAD and tolerances are set, machined or printed product often deviates. Thus you need to check machining/printing quality before starting (create 5x5x5 mm cube with printer and measure actual size, then adjust CAD).

**Next**  
- Retrieve prints of shroud and tube, and assemble.

---

## 08-14-2025

**Done**  
- Retrieved print of shroud and tube. Added 6-32 screws and inserts to the mate between tube flange and lid recess.
- Shroud print had stray filament, so I sanded down rough areas.
- Drilled hole through lid and tube bottom to allow for mic wires to pass through.
- Shroud fit well into tube, but the shroud mouth was turned rather than straight on due to fit with the tube profile. Redesigned tube in SolidWorks to ensure shroud mouth points straight.

<p float="left">
  
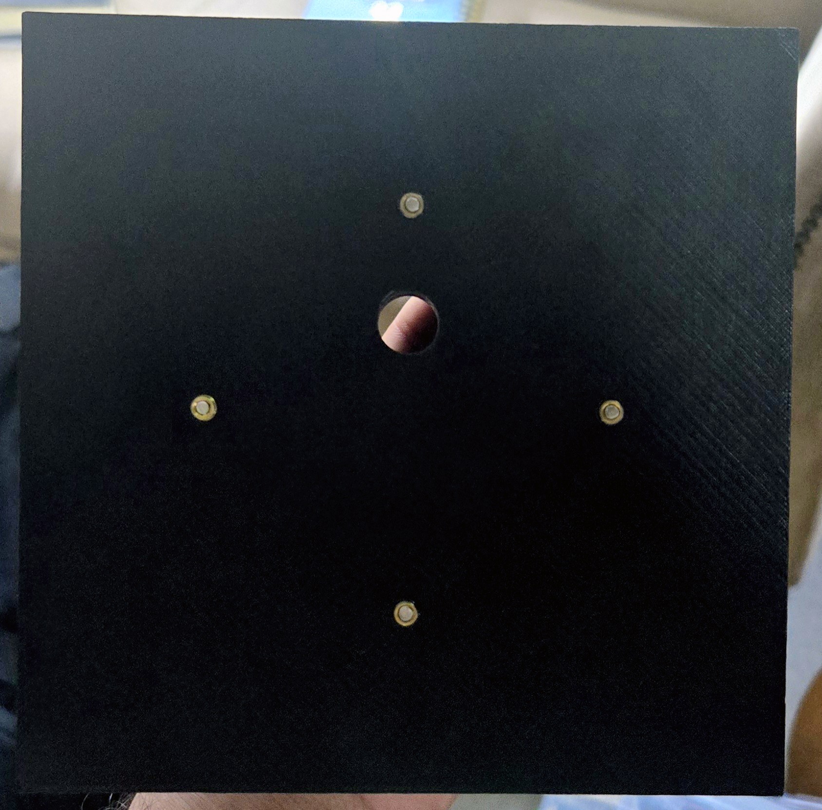
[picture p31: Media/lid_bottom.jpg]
  
  
</p>

**Learned**  
- Even though GD&T is conducted on CAD and tolerances are set, machined or printed product often deviates. Thus you need to check machining/printing quality before starting (create 5x5x5 mm cube with printer and measure actual size, then adjust CAD).

**Next**  
- Reprint tube and refit with shroud.

---

## 08-21-2025

**Done**  
- Reprinted second tube and fit properly with shroud. Began print of front and back fan housing plates. Repainted shroud with black paint to cover sanding marks. Unscrewed previous tube from lid and attached new one. 

**Learned**  
- Sanding causes markings on plastic. 

**Next**  
- Fit fan into plates and press fit into shroud.

---

## 08-27-2025

**Done**  
- Retrieved prints of plates and mounted to fan using M5 machine screws and wing nuts. Press fitted very well into shroud!

<p float="left">
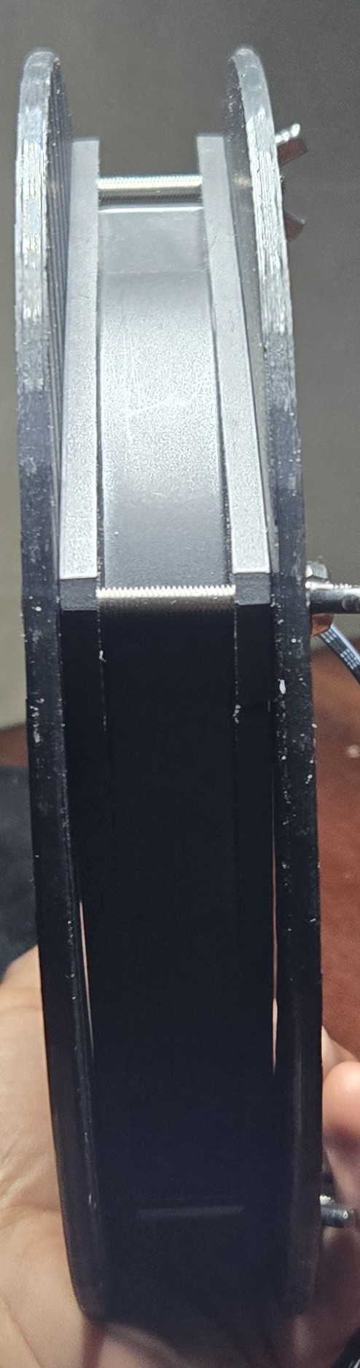
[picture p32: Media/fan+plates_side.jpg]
  
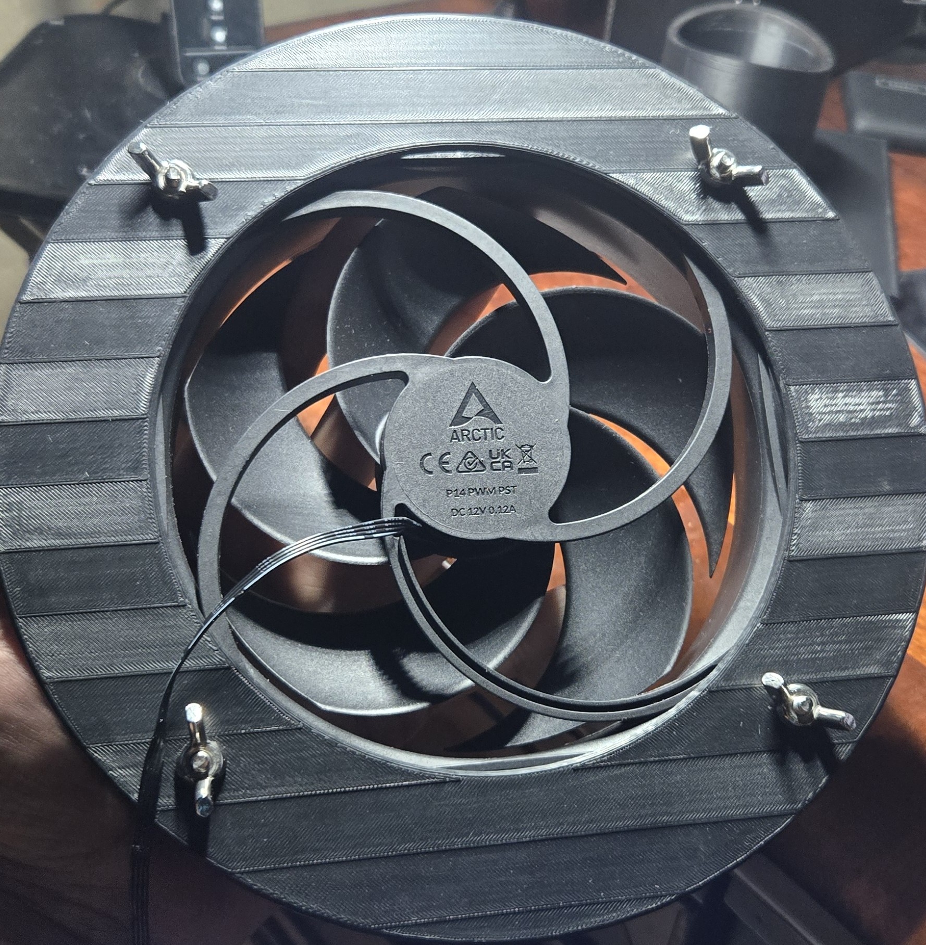
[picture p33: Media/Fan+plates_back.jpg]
  
</p>

**Learned**  
- Sanding causes markings on plastic. Polishing/repainting may be necessary.  

**Next**  
- Begin Bench Testing!

---

## 09-02-2025

**Done**  
- Began bench testing. Assembled Teensy 4.1 on breadboard, 12V barrel jack adapter, microphone module, amplifier module, and speaker.
- Cut and stripped wires at the barrel jack. Split neutral wire and soldered in a Y config. The first wire from the wall plug goes to a common junction connected to the breadboard GND rails. The second wire from the split goes to the fan plug negative terminal.
- Soldered blue and red jumper wires to the 12V supply hot and neutral wires to power the fan.
- Soldered mic module to jumper wires and plugged into breadboard (SEE WIRING DIAGRAM).
- Attached speaker to amp module using jumper wires.

<p float="left">
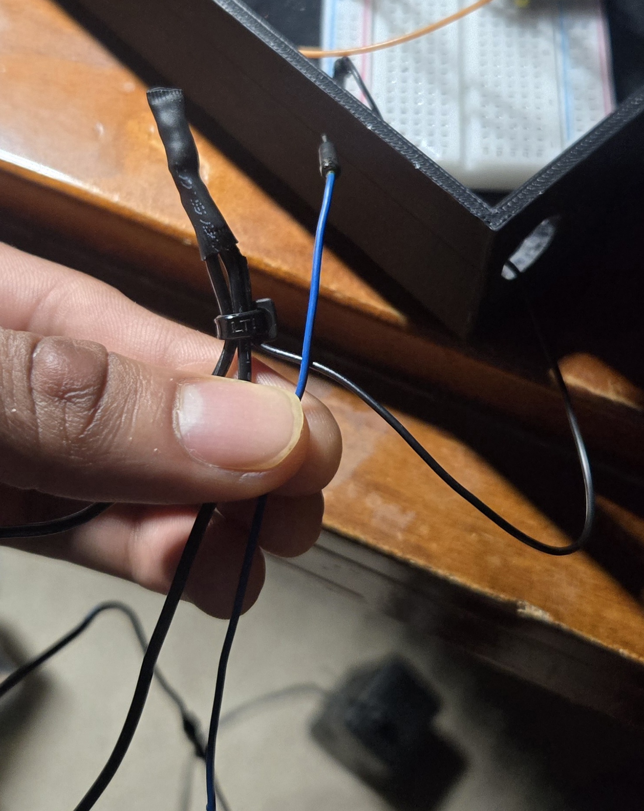
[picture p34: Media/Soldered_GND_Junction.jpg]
  
  
  
  
</p>

**Next**  
- Continue bench testing.

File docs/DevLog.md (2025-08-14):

# Noise-Canceling Fan DevLog

Welcome to the Noise-Canceling Fan DevLog! This is a running summary of daily work on this project.

---

**LINKS**  
[README](../README.md)  
[Project Specifications](Spec.md)  

---

## 06-16-2025 (Mon)

**Done**  
- Created Repo and README  
- Brainstormed high-level design: 3D printed hollow rectangular base with four supports, speaker on the front face, microphone hole on the top face, fan housed in horizontal cylinder supported by cylindrical column from base. Electrical housed under the base.

**Learned**  
- GitHub repo organizations for engineering projects.

**Next**  
- Order parts (mic, speaker, Teensy, etc), CAD practice, write project specifications.

---

## 06-17-2025 (Tues)

**Done**  
- Ordered parts (microcontroller, fan, electronics)

**Learned**  
- Electronics required (amplifier module, barrel jack adapter, etc)

**Next**  
- Write spec, BOM, CAD practice

---

## 06-19-2025 (Thur)

**Done**  
- Got hung up on internship work. Watched one SolidWorks recap video.

**Next**  
- CAD practice, first models.

---

## 06-20-2025 (Fri)

**Done**  
- Completed SolidWorks recap video

**Learned**  
- Reviewed SolidWorks basics (sketching, boss/revolve, shell, fillet)

**Next**  
- Begin practice parts

---

## 06-22-2025 (Sun)

**Done**  
- Created horizontal “lampshade” example from SolidWorks part modeling tutorial utilizing sketch, extrude, extrude-cut, shell, and fillet.  
  - [Practice_Lampshade.SLDPRT](../CAD/Practice_CAD/Practice_Lampshade.SLDPRT)
  - Lampshade screenshot 
- Created circular baseplate to practice HoleWizard
  - [Practice_Plate.SLDPRT](../CAD/Practice_CAD/Practice_Plate.SLDPRT)
  - Practice Plate screenshot

**Learned**  
- More thorough review of SolidWorks basics and learned about HoleWizard.

**Next**  
- Continue practice parts

---

## 06-23-2025 (Mon)

**Done**  
- Revisited design. Original model with speaker on front of base was deemed nonfunctional. Learned that noise canceling needs good alignment of fan noise to noise canceling output from speaker. Redesigned to include speaker pointing directly into cylindrical fan shroud. Brainstormed horizontal plate that separates direct line of sight from speaker to mic inside shroud chamber.

**Learned**  
- [AMCA Basics of Fan Noise Presentation](https://www.amca.org/assets/resources/public/assets/uploads/FINAL-_AMCA_Fan_Noise_RG.pdf)
- [Noise Canceling Case Study](https://www.diva-portal.org/smash/get/diva2%3A831430/FULLTEXT01.pdf)
-  Design requires **iteration**. Every single idea/design will have issues that come up and need to be addressed.

**Next**  
- Begin CAD for base, support tube, and shroud

---

## 06-24-2025 (Tues)

**Done**  
- Began base: 160 × 160 × 25 mm with a 5.5 mm thick lip running along the inner face of box for lid to sit flush.
  - box prelim outline

**Learned**  
- How to insert planes.

**Next**  
- Continue CAD for base, begin support tube, cylindrical shroud, round sleeve for fan.

---

## 06-27-2025 (Fri)

**Done**  
- Completed prelim design for base box. Used cut extrude from various planes within the box to create a lip on inside edge that will allow lid to sit flush with top.
  - box 6/27

**Learned**  
- Learned how to insert plane at specific height. 

**Next**  
- Begin CAD for lid, support tube, and shroud

---

## 06-30-2025 (Mon)

**Done**  
- Completed design for lid (157.5 × 157.5 × 6.5 mm). Thickness allows flange from tube to sit into lid comfortably.
- Completed design for support tube: 70 × 70 mm cylinder with 3 mm wall thickness. Added 82 mm diameter, 2.5 mm thick flange around bottom of tube. Added 82 mm diameter, 2.5 mm deep recess into lid to allow tube to fit. Added four M4 tapped holes on a 76 mm diameter circle to flange, and clearance holes for brass inserts.
   Lid+support tube 6/30

**Learned**  
- Refreshed skills with basic extrude. Began GD&T, designing one part to fit into another.  
- Refreshed skills with HoleWizard. Learned screw size selection and technique for press fitting brass inserts.

**Next**  
- Begin CAD for fan housing plates and shroud

---

## 07-01-2025 (Tues)

**Done**  
- Created circular plates for front and back of fan to fit into cylindrical shroud.   
  - OD: 208 mm, thickness: 4 mm.  
  - Hole pattern: 4 × 4.45 mm holes on 124 × 124 mm square. Front plate counterbored (Ø 8 mm) for flush screws. Back plate holes Ø 5.7 mm × 3.5 mm deep with 0.5 mm skin for brass inserts.  
  - Central cutout: Ø 140 mm, filleted inner edges, chamfered outer edges (0.5 mm × 45°).
  - [Fan_Front_Plate.SLDPRT](../CAD/Project_CAD/Fan_Front_Plate.SLDPRT)
  - Fan Front Plate FINAL
  - [Fan_Back_Plate.SLDPRT](../CAD/Project_CAD/Fan_Back_Plate.SLDPRT)
  - Fan Back Plate FINAL

**Learned**  
- How to apply real-world dimensions (fan specs) to a CAD problem.

**Next**  
- Begin CAD for shroud

---

## 07-02-2025 (Wed)

**Done**  
- Revisited box design: inner lip was only 3.5 mm, not 6.5 mm. Revised box depth to 35 mm. Fixed wall thickness (3 mm intended) by revising lid to 153.5 × 153.5 mm and changing extrude cut dimensions on box.
- Added cylindrical 8mm support feet to box base for rubber feet coverings  
- Began shroud development: finalized component dimensions within shroud (baffle, speaker, mic, plates, stopper ring). Shroud thickness: 3 mm.
- [Box_FINAL.SLDPRT]((../CAD/Project_CAD/Box.SLDPRT)
- [Box FINAL](https://github.com/vyas0028/Yashodev_Vyas_Noise-Canceled-Fan/blob/main/Media/Box_Final.png?raw=true)

**Learned**  
- Revisiting previously completed parts is important—design and dimensions may change based on interactions.

**Next**  
- Continue shroud development and figure out mate with vertical tube.

---

## 07-05-2025 (Fri)

**Done**  
- Cleaned up project documentation. Filled in missing entries.

**Learned**  

**Next**  
- Continue shroud development and figure out mate with vertical tube.

---

## 07-08-2025 (Tue)

**Done**  
- Further developed shroud design. Created baffle that blocks direct line of sight from speaker at top of shroud to mic at bottom. Drafted speaker hole on top of shroud: created boss on angled plane, then extruded cut flush to create speaker pocket.
  shroud with blocking baffle
- Shroud with initial extrusion

**Learned**  
- How to angle planes and insert reference features (axes, planes) in relation to other features.
  
**Next**  
- Continue shroud development and figure out mate with vertical tube.

---

## 07-09-2025 (Wed)

**Done**  
- Further developed shroud design. Finalized extruded cut to form speaker ledge wihtin top extrusion. Ensured that a 60 degree projection from the fan center does not hit the shielding baffle. This prevents reflection and excess vibrations. Reflections and subsequent comb filtering can result in reverberations and poor ANC.
- Shroud with initial extrusion
- Speaker 60-deg cone avoiding baffle

**Learned**  
- [Basics of comb filtering](https://www.dpamicrophones.com/mic-university/audio-production/the-basics-about-comb-filtering-and-how-to-avoid-it/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)
- reflections and reverberations are harmful.
  
**Next**  
- Continue shroud development and figure out mate with vertical tube.

---

## 07-10-2025 (Wed)

**Done**  
- Further developed shroud design. Finalized extruded cut to form speaker ledge wihtin top extrusion. Ensured that a 60 degree projection from the fan center does not hit the shielding baffle. This prevents reflection and excess vibrations. Reflections and subsequent comb filtering can result in reverberations and poor ANC.
- Shroud with initial extrusion
- Speaker 60-deg cone avoiding baffle

**Learned**  
- [Basics of comb filtering](https://www.dpamicrophones.com/mic-university/audio-production/the-basics-about-comb-filtering-and-how-to-avoid-it/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)
- reflections and reverberations are harmful.
  
**Next**  
- Continue shroud development and figure out mate with vertical tube.

## 07-11-2025 (Thurs)

**Done**  
- Finalized shroud design. Added 15 mm diameter circular recess in bottom of shroud for microphone array. Extrude cut hole for microphone wiring that goes into tube and down into base. Decided on two piece shroud and tube. Shroud has extrusion on the bottom that fits into the tube and will be glued.
- Compiled tube and shroud into an assembly. Changed extrusion of tube to "up to next" to get it flush with the shroud.
- Final Assembly
- Shroud Side View
- Tube + shroud mate

**Learned**  
- Extrude "up to next" is very useful for getting features flush with one another.
- Consulted coworker on one piece vs two piece shroud + tube. One piece would have wasted a lot of support material.
  
**Next**  
- Continue Prints! .

## 07-14-2025-07/21/2025 (Thurs)

**Done**  
- On vacation, updated resume, documentation. 

## 07-22-2025 (Thurs)

**Done**  
- Retrieved prints and physically fit together lid and base. Lid was slighly smaller than base lip area, so purchased set screw from Menards and heat set insert into base.
- Began print of shroud and initial tube.

**Learned**  
- Asked R&D Technician at my internship about tolerance and sizing issue:
  - Even though GD&T is conducted on CAD and tolerances are set, machined or printed product often deviates. Thus you need to check machining/printing quality before starting (create 5x5x5 mm cube with printer and measure actual size, then adjust CAD).
- 
  
**Next**  
- Retrieve prints of shroud and tube, and assemble.

## 07-22-2025 (Fri)

**Done**  
- Retrieved print of shroud and tube. Added 6-32 screws and inserts to the mate between tube flange and lid recess. 
- Shroud print had stray filament, so I sanded down rough areas.
- Drilled hole through lid and tube bottom to allow for mic wires to pass through.
- Shroud fit well into tube, but the shroud mouth was turned rather than straight on due to fit with the tube profile. Redesigned tube in SolidWorks to ensure shroud mouth points straight.
- tube+lid
- Lid_bottom
- Lid_bottom_side

**Learned**  
- Asked R&D Technician at my internship about tolerance and sizing issue:
  - Even though GD&T is conducted on CAD and tolerances are set, machined or printed product often deviates. Thus you need to check machining/printing quality before starting (create 5x5x5 mm cube with printer and measure actual size, then adjust CAD).
- 
  
**Next**  
- Reprint tube and refit with shroud

## 07-25-2025 (Fri)

**Done**  
- Reprinted second tube and fit properly with shroud. Began print of front and back fan housing plates. Repainted shroud with black paint to cover sanding marks. Unscrewed previous tube from lid and attatched new one. 

**Learned**  
- Sanding causes markings on plastic. 

**Next**  
- Fit fan into plates and press fit into shroud.

## 07-27-2025 (Fri)

**Done**  
- Retrieved prints of plates and mounted to fan using m5 machine screws and wing nuts. Press fitted very well into shroud!
- plates_side
- plates_back

**Learned**  
- Sanding causes markings on plastic. Polishing/repainting may be nesesscary.  

**Next**  
- Begin Bench Testing!

## 07-29-2025 (Fri)

**Done**  
- Began bench testing. Assembled teensy 4.1 on breadboard, 12V barrel jack adapter, microphone module, amplifier module, and speaker. Cut and stripped wires at the barrel jack. Split neutral wire and soldered in a Y config. The first wire from the wall plug goes to a common junction connected to the breadboard GND rails. The second wire from the split goes to the fan plug negative terminal.
- Soldered blue and red jumper wires to the 12V supply hot and neutral wires to power the fan.
- Soldered mic module to jumper wires and plugged into breadboard (SEE WIRING DIAGRAM)
- Attatched speaker to amp module using jumper wires.
- GND junction
- fan power wires
- soldered mic
- soldered amp

**Learned**  
- Sanding causes markings on plastic. Polishing/repainting may be nesesscary.  

**Next**  
- Begin Bench Testing!

```

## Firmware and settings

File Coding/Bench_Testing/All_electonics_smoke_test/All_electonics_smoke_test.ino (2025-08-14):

/**********************************************************************
 *  Bench 1  –  Mic ↔ Speaker Smoke-Test + Tone Burst   (Teensy 4.1)
 *  Cycle: 0-4 s mic passthrough • 4-8 s 1 kHz sine • 8-10 s silence
 *         10-12 s fan PWM sweep on pin 6, then repeat
 *********************************************************************/
#include <Audio.h>
#include <Wire.h>
#include <SPI.h>

/* ── Audio graph ────────────────────────────────────────────────── */
AudioInputI2S        mic;        // INMP441
AudioSynthWaveform   osc;        // 1 kHz sine
AudioMixer4          mix;        // ch0 = mic, ch1 = osc
AudioOutputI2S       spk;        // → MAX98357A DIN (pin 7)
AudioConnection      pc1(mic, 0, mix, 0);
AudioConnection      pc2(osc, 0, mix, 1);
AudioConnection      pc3(mix, 0, spk, 0);
AudioControlSGTL5000 dummy;      // required by Audio lib

/* ── Fan PWM ───────────────────────────────────────────────────── */
const uint8_t FAN_PIN = 6;
const uint16_t PWM_HZ = 25000;   // 25 kHz carrier

/* ── Timers ────────────────────────────────────────────────────── */
elapsedMillis tCycle, tPWM;

void setup() {
  pinMode(LED_BUILTIN, OUTPUT);

  /* audio */
  AudioMemory(12);
  osc.begin(0.5f, 1000.0f, WAVEFORM_SINE);  // gain, Hz, shape
  mix.gain(0, 1.0f);   // mic on
  mix.gain(1, 0.0f);   // osc muted
  for (int i = 2; i < 4; ++i) mix.gain(i, 0);

  /* fan PWM */
  analogWriteFrequency(FAN_PIN, PWM_HZ);
  analogWriteResolution(8);      // duty 0-255
  analogWrite(FAN_PIN, 0);

  Serial.begin(115200);
  Serial.println(F("Bench 1: compile-tested, ready to run."));
}

void loop() {
  /* 12-s state machine */
  if (tCycle < 4000) {                   // 0–4 s MIC
    mix.gain(0, 1.0f);  mix.gain(1, 0.0f);
  } else if (tCycle < 8000) {            // 4–8 s 1 kHz
    mix.gain(0, 0.0f);  mix.gain(1, 1.0f);
  } else if (tCycle < 10000) {           // 8–10 s silence
    mix.gain(0, 0.0f);  mix.gain(1, 0.0f);
  } else if (tCycle < 12000) {           // 10–12 s fan sweep
    if (tPWM >= 250) {                   // step every 0.25 s
      static int duty = 0;
      duty = (duty + 64) & 1000;          // 0→64→128→192→0
      analogWrite(FAN_PIN, duty);
      tPWM = 0;
    }
  } else {                               // restart cycle
    tCycle = 0;  tPWM = 0;  analogWrite(FAN_PIN, 0);
  }

  /* heartbeat LED: 0.5 s blink */
  digitalWriteFast(LED_BUILTIN, (tCycle / 500) & 1);
}

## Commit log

2025-06-19 Created spec sheet and BOM
    [BOM.xlsx]
2025-06-30 Updated readme, added cad parts.
    [Practice_Lampshade.SLDPRT, Practice_Plate.SLDPRT, box.SLDPRT]
2025-07-13 design and image updates
    [Assem2.SLDASM, Assem2.SLDPRT, Assem4.SLDASM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]
2025-07-13 chore(media): remove practice cad folder from docs
2025-07-13 chore(docs): insert images into devlog
2025-07-13 chore(media): added lid+tube png
2025-07-14 chore(media): Added front plate png
2025-07-14 chore(media): fan back plate image
2025-07-15 chore(media): add images
    [Shroud.SLDPRT]
2025-07-15 chore(media): add tube + shroud mate png
2025-08-02 chore(docs): documentation update
    [Assem4.SLDASM, BOM.xlsx, Mic_Fixture.SLDPRT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]
2025-08-14 chore(CAD): documentation update
    [Assem2.SLDPRT, Assem8.STL, Fan_Back_Plate.STL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]
2025-09-05 chore(media):add jpg
    [X_section.SLDASM]
